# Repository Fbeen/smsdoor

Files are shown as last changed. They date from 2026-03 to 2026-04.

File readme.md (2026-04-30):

# SMSDOOR – GSM + WiFi Door & Roller Shutter Controller  
(RP2040 + A7670E + Pico W)

SMSDOOR is a hybrid GSM (SMS) and via WiFi Access Point configurated door and roller shutter controller based on a Raspberry Pi Pico / Pico W (RP2040) and a SIMCom A7670E 4G modem.

The system allows authorized users to control a roller shutter or overhead garage door via:
- SMS
- Built-in WiFi web interface
- Serial console

---

# Features

## Control
- Roller shutter control (UP / DOWN)
- Overhead garage door control (DOWN)
- Control via SMS, Web UI, or Console

## Connectivity
- LTE modem (SMS control)
- WiFi Access Point (Pico W)
- Built-in webserver (mobile friendly UI)

---

# Hardware

## Main components
- Raspberry Pi Pico / Pico W
- SIMCom A7670E LTE modem
- Relay outputs
- External 5V power supply (2–3A recommended)

## ⚠️ Power note

WiFi + LTE modem can cause current spikes.  
Use a stable 5V / 2A–3A supply. PC USB is often not sufficient.

---

# UART connections

| Function | Pico Pin |
|---|---|
| Debug TX | GP0 |
| Debug RX | GP1 |
| Modem TX | GP20 |
| Modem RX | GP21 |

---

# Build

    mkdir build
    cd build
    cmake ..
    ninja

---

# First Start

Send SMS:

    INIT

Sender becomes admin.

---

# Commands

## Door

    UP                  Roller shutter up
    DOWN                Roller shutter down
    OVERHEAD DOWN       Close overhead door
    CLOSEAT <hh:mm>     Auto close roller shutter and  overhead door daily on a given time
    CLOSEAT OFF         auto close off

---

# Phonebook

    ADD +31612345678    adds a phonenumber to the phonebook
    DEL +31612345678    deletes a phonenumber from the phonebook
    LIST                lists all phonenumbers 

---

# Admin

    PROMOTE +31612345678    promote a number to an administrator
    DEMOTE +31612345678     demote a number to a normal user (only open/close)

---

# System

    PIN <code> *        Set a new PIN code to unlock the SIM card
    SIDD <name>         Set a new SSID for the WiFi AP
    PASS <passwd>       Set a new password for the WiFi AP
    AT <command> *      Send a command directly to the A7670E modem
    INFO                gives some system information
    LOG                 gives a log about most important events
    HELP                gives help information
    WIFI ON/OFF         switch on the WiFi AP for 15 minutes or switches off

---

# WiFi & Web Interface

- Access point (default 192.168.4.1)
- Mobile UI
- Door control and system information
- User management
- Settings configuration
- Console (live log)
- Help page

---

# Notes

- Non-blocking firmware
- Flash storage
- Designed for stability

---

# Author

Frank Beentjes  
https://github.com/Fbeen

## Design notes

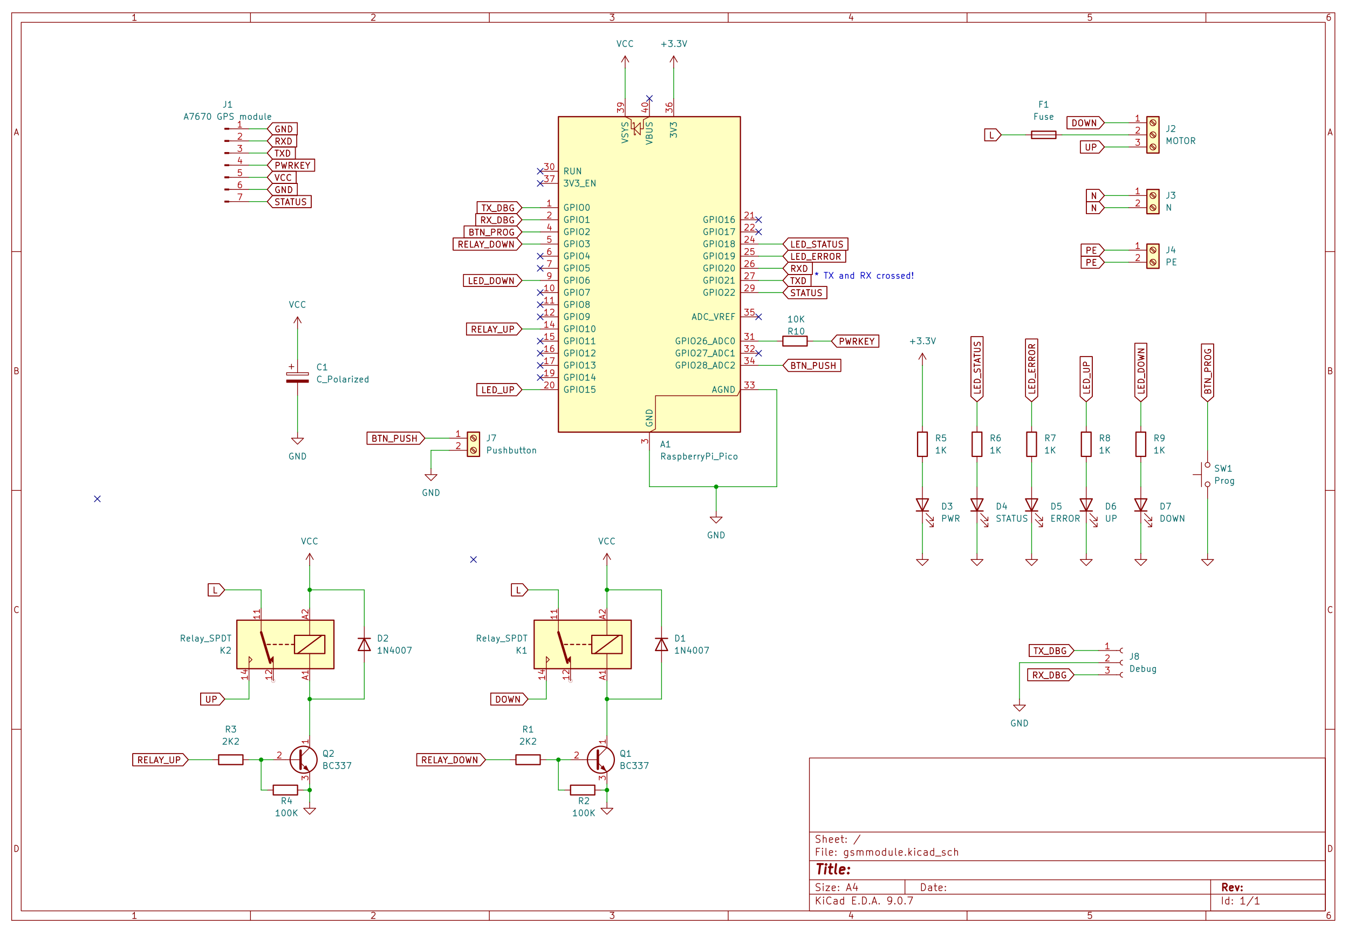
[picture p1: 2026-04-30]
hardware/schema.png

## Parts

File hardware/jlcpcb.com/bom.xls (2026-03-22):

Comment | Designator | Footprint | JLCPCB Part #
680 | R5 | R0805 | C17798
680 | R6 | R0805 | C17798
680 | R7 | R0805 | C17798
680 | R8 | R0805 | C17798
680 | R9 | R0805 | C17798
error | D5 | 0805 | C2295
down | D7 | 0805 | C2295
100K | R2 | R0805 | C22356675
100K | R4 | R0805 | C22356675
10K | R10 | R0805 | C22356686
2K2 | R1 | R0805 | C17520
2K2 | R3 | R0805 | C17520
up | D6 | 0805 | C2297
power | D3 | 0805 | C2296
status | D4 | 0805 | C2293

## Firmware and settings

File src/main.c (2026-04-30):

#include <stdio.h>
#include <string.h>
#include <ctype.h>
#include "pico/stdlib.h"
#include "hardware/watchdog.h"
#include "hardware/timer.h"
#include "hardware/uart.h"
#include "webserver.h"
#include "console.h"
#include "phonebook.h"
#include "hardware.h"
#include "commands.h"
#include "modem.h"
#include "util.h"
#include "clock.h"
#include "rshutter.h"
#include "led.h"

/* ----------------------------------------------------------
   TIMER
   ---------------------------------------------------------- */

static struct repeating_timer timer;

/* This function is called every tenth of a second (ISR context) */
bool timer_callback(struct repeating_timer *t)
{
    clock_tick();       /* see clock.c    */
    rshutter_tick();    /* see rshutter.c */
    led_tick();         /* see led.c      */

    return true;        /* repeat timer   */
}

/* ----------------------------------------------------------
   MAIN
   ---------------------------------------------------------- */

int main()
{
    /* enable watchdog, pico restarts if things go wrong */
    watchdog_enable(30000, 1);  // 15 seconds watchdog

    /* enable standard pico stuff */
    stdio_init_all();

    /* load config from flash*/
    config_init();

    /* sets the gpio's, see hardware.c */
    gpio_setup();

    /* Start repeating hardware timer */
    add_repeating_timer_ms(ISR_REPEAT_MS, timer_callback, NULL, &timer);

    /* flash status led during init */
    led_activate(GPIO_LED_STATUS, 500, 0); 

    /* setup uart to console and uart to modem */
    uart_setup();
    sleep_ms(2000);

    cprintf("\n[TC] Pico Rolluik Controller v%s starting...\n", VERSION);
    cprintf("[TC] Type \"HELP\" voor hulp!\n");

    /* loads the phonenumber whitelist from flash */
    phonebook_init();

    /* webserver driver init, does not start the webserver */
    ws_stack_init();

    watchdog_update();

    /* init modem, see modem.c */
    modem_init();

    while (1)
    {
        /* tasks to do */
        console_uart_task();    /* see console.c  */
        modem_uart_task();      /* see modem.c    */
        clock_task();           /* see clock.c    */
        rshutter_task();        /* see rshutter.c */
        wifi_task();            /* see webserver.c */

        tight_loop_contents();
        watchdog_update();
    }
}

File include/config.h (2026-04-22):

#ifndef CONFIG_H
#define CONFIG_H

#include <stdint.h>

/* version info */
#define VERSION "1.0"

/* Size of the buffer used to store incoming lines from the modem
Used for AT command responses, SMS messages, and status lines */
#define LINE_BUFFER_SIZE    128

/* Maximum length of a phone number string including '+' and null terminator
Example: "+31612345678" */
#define PHONENR_SIZE        16

/* Maximum number of phone numbers stored in the internal phonebook
These numbers are allowed to control the system */
#define MAX_PHONES          16

/* Maximum length of a received command string
Used for SMS commands or serial console commands like ADD, DEL, LIST */
#define COMMAND_SIZE        32

/* ISR time interval in milliseconds */
#define ISR_REPEAT_MS       100

#define FLASH_TOTAL_SIZE       (2 * 1024 * 1024)

#define FLASH_CONFIG_OFFSET    (FLASH_TOTAL_SIZE - FLASH_SECTOR_SIZE)
#define FLASH_PHONEBOOK_OFFSET (FLASH_TOTAL_SIZE - 2 * FLASH_SECTOR_SIZE)

#define WIFI_SSID_SIZE          33   // 32 + null
#define WIFI_PASS_SIZE          64   // 63 + null

#define CONFIG_MAGIC            0x43464731   // "CFG1"
#define CONFIG_VERSION          4

#define SIM_PIN_SIZE            8

typedef struct
{
    uint32_t magic;
    uint16_t version;
    uint16_t close_time; //  in minutes per day ( 0 .. 1439 )

    char reserved;
    char ssid[WIFI_SSID_SIZE];
    char pass[WIFI_PASS_SIZE];

    char sim_pin[SIM_PIN_SIZE];

    uint16_t duration_shutter; // the duration that the relay of the roller shutter is switched on in seconds
    uint16_t duration_overhead; // the duration that the relay of the overheaddoor is switched on in seconds

} config_t;

extern config_t cfg;

#define CLOSE_DISABLED 0xFFFF

void config_init();
void config_save();
void config_set_pin(const char *pin);
void config_set_ssid(const char *ssid);
void config_set_pass(const char *pass);

#endif

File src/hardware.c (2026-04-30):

#include "pico/stdlib.h"
#include "hardware/uart.h"
#include "hardware/gpio.h"
#include "hardware.h"

/* ----------------------------------------------------------
   UART
   ---------------------------------------------------------- */

void uart_setup()
{
    // Debug UART
    uart_init(UART_DEBUG, UART_BAUDRATE);
    gpio_set_function(UART_DEBUG_TX, GPIO_FUNC_UART);
    gpio_set_function(UART_DEBUG_RX, GPIO_FUNC_UART);

    // Modem UART
    uart_init(UART_MODEM, UART_BAUDRATE);
    gpio_set_function(UART_MODEM_TX, GPIO_FUNC_UART);
    gpio_set_function(UART_MODEM_RX, GPIO_FUNC_UART);
}

void gpio_setup()
{
    gpio_init(GPIO_LED_STATUS);
    gpio_set_dir(GPIO_LED_STATUS, GPIO_OUT);

    gpio_init(GPIO_LED_ERROR);
    gpio_set_dir(GPIO_LED_ERROR, GPIO_OUT);

    gpio_init(GPIO_RELAY_UP);
    gpio_set_dir(GPIO_RELAY_UP, GPIO_OUT);

    gpio_init(GPIO_RELAY_DOWN);
    gpio_set_dir(GPIO_RELAY_DOWN, GPIO_OUT);

    gpio_init(GPIO_LED_UP);
    gpio_set_dir(GPIO_LED_UP, GPIO_OUT);

    gpio_init(GPIO_LED_DOWN);
    gpio_set_dir(GPIO_LED_DOWN, GPIO_OUT);

    /* overhead door */
    gpio_init(GPIO_OVERHEAD );
    gpio_disable_pulls(GPIO_OVERHEAD );  // important!
    gpio_set_dir(GPIO_OVERHEAD , GPIO_IN);   // high-Z

    /* push button */
    gpio_init(GPIO_BUTTON);
    gpio_set_dir(GPIO_BUTTON, GPIO_IN);
    gpio_pull_up(GPIO_BUTTON);
}

void roldeur_down_press()
{
    gpio_set_dir(GPIO_OVERHEAD , GPIO_OUT);
    gpio_put(GPIO_OVERHEAD , 0);   // press button
}

void roldeur_down_release()
{
    gpio_set_dir(GPIO_OVERHEAD , GPIO_IN);   // high-Z
}

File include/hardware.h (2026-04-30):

#ifndef HARDWARE_H
#define HARDWARE_H

#define UART_DEBUG      uart0
#define UART_MODEM      uart1

#define UART_DEBUG_TX   0
#define UART_DEBUG_RX   1

#define UART_MODEM_TX   20
#define UART_MODEM_RX   21

#define UART_BAUDRATE   115200

#define GPIO_RELAY_UP   10
#define GPIO_RELAY_DOWN 3

#define GPIO_LED_UP     15
#define GPIO_LED_DOWN   6
#define GPIO_LED_STATUS 18
#define GPIO_LED_ERROR  19
#define GPIO_LED_PICO   25

#define GPIO_OVERHEAD   28

#define GPIO_BUTTON     2

/* output pins */

void uart_setup();
void gpio_setup();


void roldeur_down_press();
void roldeur_down_release();

#endif

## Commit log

2026-03-29 led improvements
2026-05-03 error on sms / wrong pin error / empty list problems
    [commands.c, modem.c, router.c]
